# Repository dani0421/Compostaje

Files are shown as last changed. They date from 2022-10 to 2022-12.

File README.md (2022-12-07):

# Proyecto de Sistemas embebidos
Este es el repositorio del proyecto (Nombre del proyecto) de la materia de Sitemas embebidos 

## Integrantes
Daniela Valentina Amaya Vargas

Diana Patricia Cortés Nava

Julian David Escobar Jamioy

## Problemática
Cada año la cantidad de residuos organicos a nivel mundial es de 11.200 millones y contribuyen un 5% a las emisiones de gases de efecto invernadero [1], esto cada año incrementa el calentamiento global, sin contar con que poco a poco los basureros alrededor del mundo estan llegando a su maxima capacidad de desechos. La mayoria de estos residuos se generan en los hogares y generalmente no son reutilizados, es por esto que nace la idea de crear (nombre del proyecto), una basurera de desechos organicos capaz de convertir los residuos en compostaje, esto permitirá que se logren reducir las emisiones de gases de efecto invernadero reutilizando los residuos organicos y convirtiendolos en tierra para abonar las plantas del hogar e incluso las plantas de una huerta.

## Objetivos
### Objetivo General:
Desarrollar un sistema embebido que permita darle un manejo óptimo a los desechos organicos de manera cómoda y sencilla, con el fin de poder ser implementado por cualquier usuario de manera doméstica. 
### Objetivos Especificos:
* Diseñar un sistema compacto que integre diseño de PCB, programación de microcontroladores como ESP32 y diseño físico del prototipo.
* Obtener un producto final comercial, en el que se tenga en cuenta también aspectos financieros incluyendo mano de obra.
* Documentar todas las etapas del proceso de creación del proyecto hasta su finalización.

## Alcance
Elaborar un (nombre del proyecto) capaz de transformar, en cada uso, un volumen no mayor a 1.76 L de residuos orgánicos en compostaje. Contará con 3 modos de acuerdo a cuan lleno se encuentre el tambor, los cuales podrán ser elegidos según usuario vea conveniente; una vez elegido un modo, la pantalla OLED indicará la temperatura, humedad y el tiempo que aun haga falta para que el compostaje esté listo y pueda ser retirado de (nombre del proyecto). 

## Requerimientos

### Requerimientos funcionales

* Seleccionar el nivel de compostaje que el dispositivo contiene.
* Visualizar por medio de pantalla el tiempo que falta para finalizar el proceso.
* Notificar al usuario cuando los filtros requieran ser reemplazados. 
* Evitar que el dispositivo genere malos olores.
* Notificar al usuario por medio de un mensaje vía Telegram cuando se acabó el proceso de compostaje.

### Requerimientos no funcionales

* El sistema requiere de un tiempo mínimo de 24 horas para realizar un proceso.

## Diagrama de bloques

Diagrama de bloques compost(4)

## Componentes

### Optoacoplador
Servira para realizar un desacople fisico entre el ESP32 y el controlador (LN298N) de nuestros motores, debido a que su voltaje de trabajo es diferente; se hara uso de la referencia TLP281 de 4 canales.
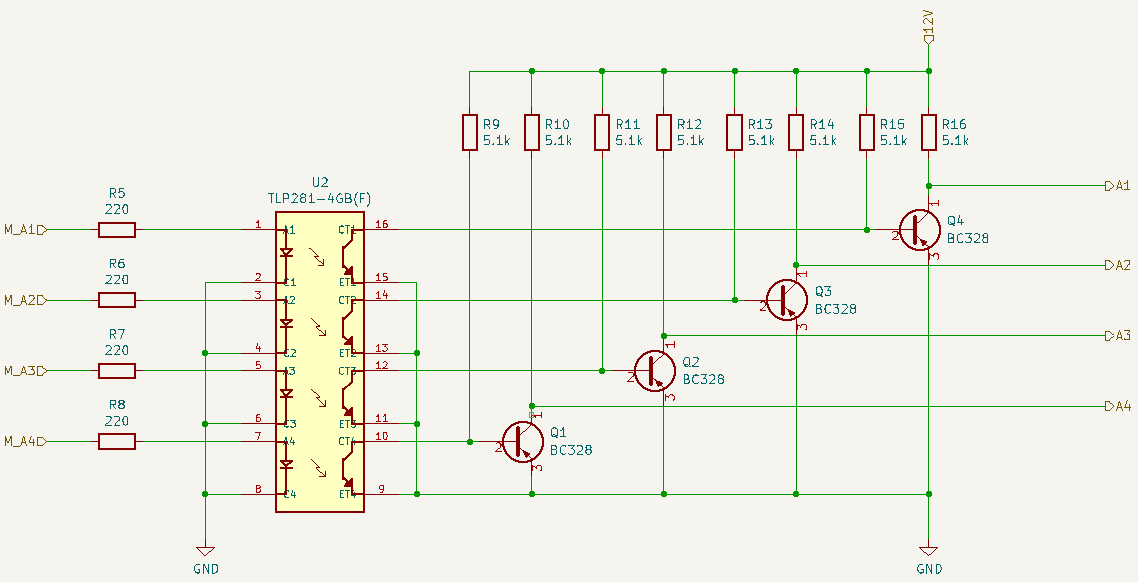
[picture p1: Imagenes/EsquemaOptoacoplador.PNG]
Esquema Optoacoplador



### Controlador de Motor
Referencia L298N que posee 4 pines de salida, teniendo en cuenta que nuestro motor es un KH56JM2U047 de bifase y con 4 pines de entrada.
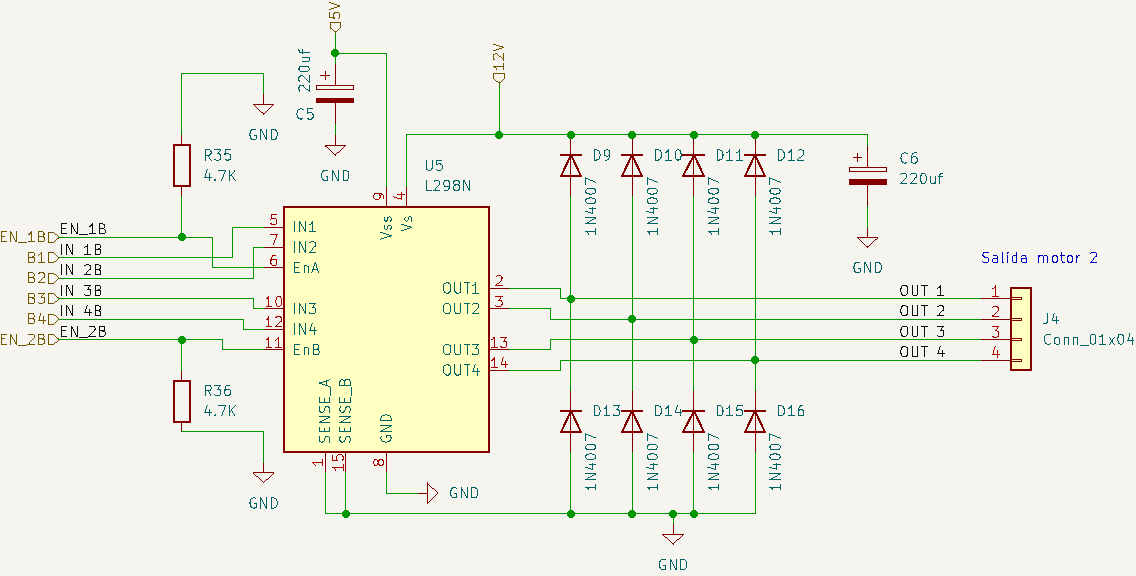
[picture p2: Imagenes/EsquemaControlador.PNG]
EsquemaControlador




### Pantalla OLED
Se usará la referencia SSD1306, la cual posee una matriz de 128x64 y cuya alimentación necesaaria es de 3.3V ([DATASHEET](https://html.alldatasheet.com/html-pdf/1179026/ETC2/SSD1306/701/6/SSD1306.html)); donde el usuario podra observar el tiempo que aun hace falta para que el compostaje este listo. Cuya dirección para I2C es 0x3C.

OLEDimagen

El SDA se conecta al pin 33 del ESP32 y el SCL al pin 36 de ESP32, cabe resaltar que en la placa no quedaran orificios para la pantalla, unicamente los pines para hacer la conexión.

### Touch
Aunque la ESP posee pines que se pueden usar como touch, se optó por hacer uso de un touch capacitivo externo, el cual nos permitirá abrir la tapa principal, que es por donde se introducira los residuos organicos junto a la tierra que posteriormente se mezclará. La referencia a usar es HW-139



### Motor Nema
Para el proceso de triturado de los residuos organicos y mezclado se usaran dos motores NEMA 17, estos son motores bipolares que pueden ser alimentados con un voltaje de 12 a 24 voltios, se opto por alimentarlos a un voltaje de 12V. 



### Servomotor

El servomotor se usara para abrir y cerrar la tapa de la basuera 


## Diseno PCB
A continuacion se muestra el diseno que se realizo para la PCB

WhatsApp Image 2022-12-06 at 11 18 50 PM
WhatsApp Image 2022-12-06 at 11 18 51 PM
WhatsApp Image 2022-12-06 at 11 18 09 PM

## Montaje fisico
Para el montaje fisico se imprimeron en 3D las siguientes piezas:

WhatsApp Image 2022-12-06 at 11 18 11 PM(2)

Luego se procedio al armado de el prototipo como se muestra en las siguientes imagenes:

WhatsApp Image 2022-12-06 at 11 18 11 PM(1)
WhatsApp Image 2022-12-06 at 11 18 10 PM
WhatsApp Image 2022-12-06 at 11 18 11 PM
WhatsApp Image 2022-12-06 at 11 18 04 PM
WhatsApp Image 2022-12-07 at 7 59 00 AM

https://user-images.githubusercontent.com/92388558/206091587-dc1af1c8-e01d-440c-9be7-15e96c51869d.mp4

## Pruebas de funcionamiento

https://user-images.githubusercontent.com/103794195/206186310-e058958a-483b-43ef-9478-b426c58254a1.mp4

## Referencias
[1] Nations, U. (2022). Datos y cifras | Naciones Unidas. Retrieved 24 August 2022, from https://www.un.org/es/actnow/facts-and-figures

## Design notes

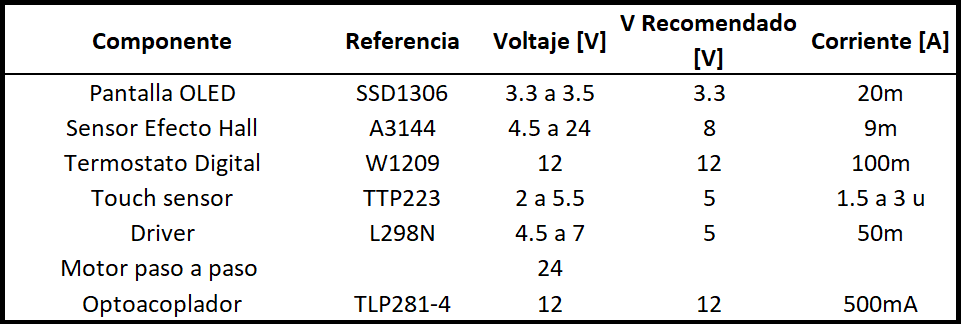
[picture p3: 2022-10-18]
Imagenes/TablaPotencia.PNG

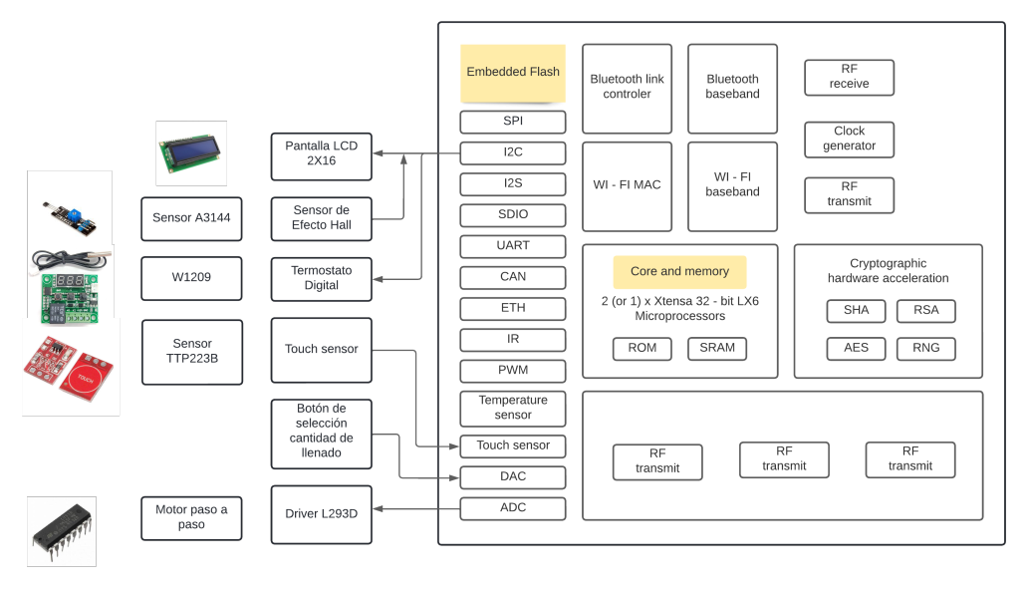
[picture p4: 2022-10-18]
Imagenes/Esquema2.PNG

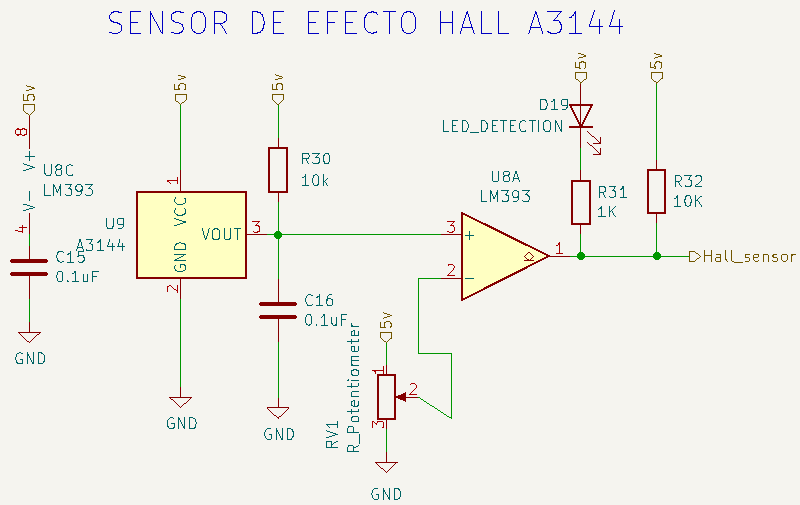
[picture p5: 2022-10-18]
Imagenes/EsquemaHall.PNG

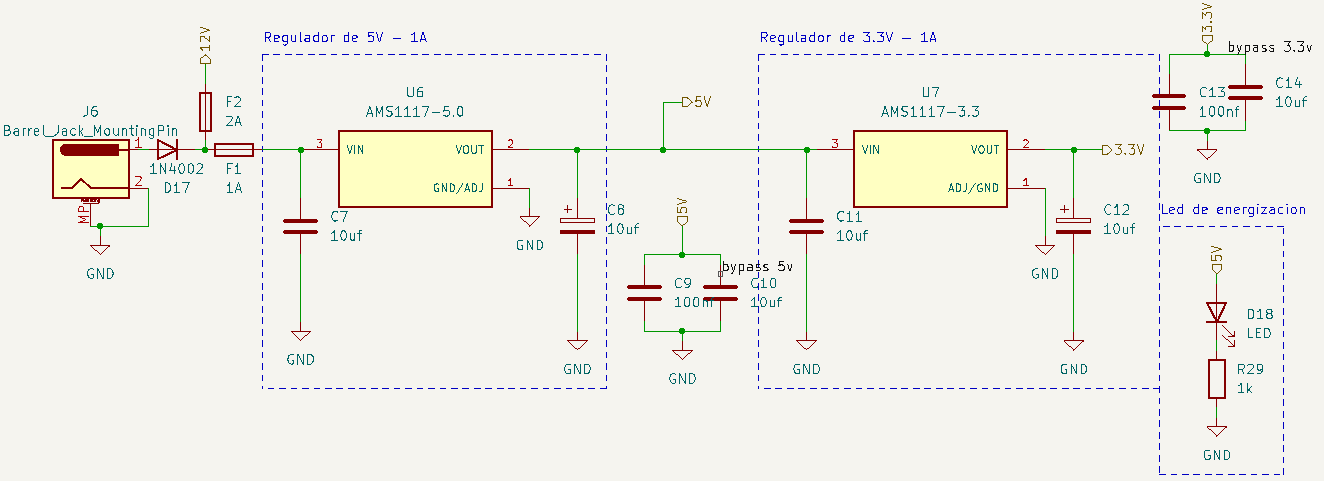
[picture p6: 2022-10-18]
Imagenes/EsquemaPotencia.PNG

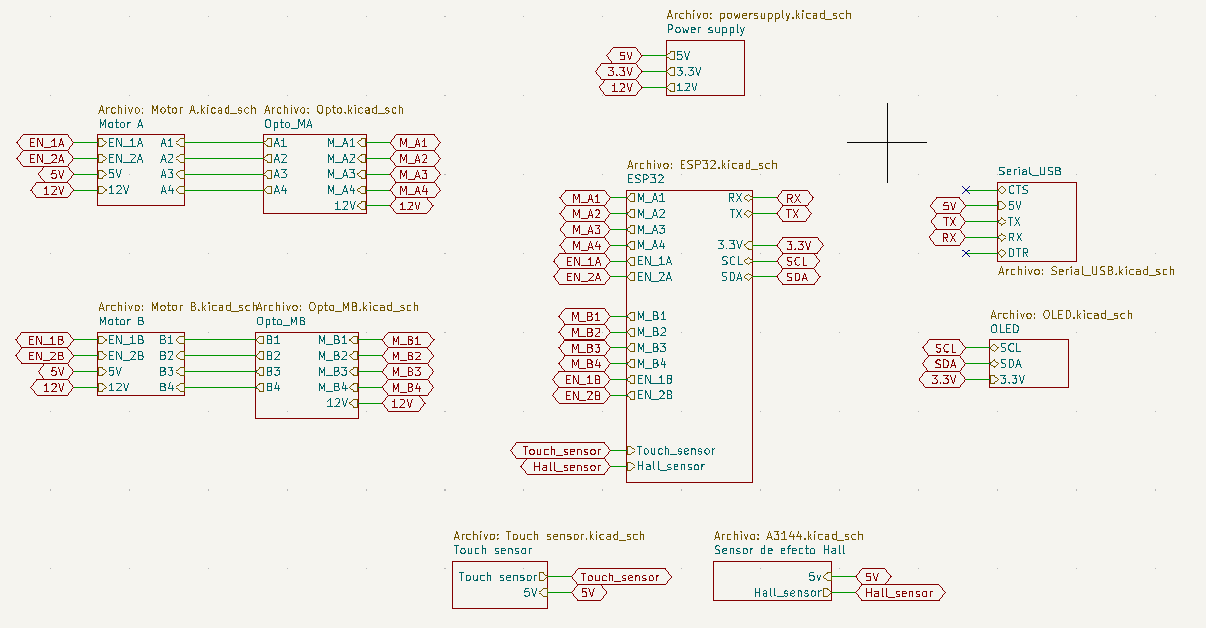
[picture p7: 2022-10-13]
Imagenes/Esquema.PNG

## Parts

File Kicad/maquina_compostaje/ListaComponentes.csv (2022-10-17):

Id | Designator | Package | Quantity | Designation | Supplier and ref
1 | C18 | C_1206_3216Metric_Pad1.33x1.80mm_HandSolder | 1 | 10uF
2 | SW2 | smd_push2 | 1 | BOOT
3 | C17,C15,C16 | C_1206_3216Metric_Pad1.33x1.80mm_HandSolder | 3 | 0.1uF
4 | R3,R2,R36,R34,R35,R33 | R_1206_3216Metric_Pad1.30x1.75mm_HandSolder | 6 | 4.7K
5 | C4,C5,C6,C3 | CP_Elec_8x10 | 4 | 220uf
6 | J2 | JST_EH_B5B-EH-A_1x05_P2.50mm_Vertical | 1 | GPIO
7 | SW1 | smd_push2 | 1 | RESET
8 | J5 | JST_EH_B3B-EH-A_1x03_P2.50mm_Vertical | 1 | TOUCH_SENSOR
9 | R4,R30,R1 | R_1206_3216Metric_Pad1.30x1.75mm_HandSolder | 3 | 10k
10 | D18 | LED_1206_3216Metric_Pad1.42x1.75mm_HandSolder | 1 | LED
11 | U9 | Allegro_SIP-3 | 1 | A3144
12 | RV1 | Potentiometer_ACP_CA6-VSMD_Vertical | 1 | R_Potentiometer
13 | J8 | JST_EH_B4B-EH-A_1x04_P2.50mm_Vertical | 1 | OLED
14 | U8 | SOIC-8_3.9x4.9mm_P1.27mm | 1 | LM393
15 | U5,U4 | TO-220-15_P2.54x2.54mm_StaggerOdd_Lead4.58mm_Vertical | 2 | L298N
16 | C2 | C_1206_3216Metric | 1 | 10uf
17 | R32 | R_1206_3216Metric_Pad1.30x1.75mm_HandSolder | 1 | 10K
18 | U1 | ESP32-WROOM-32 | 1 | ESP32-WROOM-32
19 | D19 | LED_1206_3216Metric_Pad1.42x1.75mm_HandSolder | 1 | LED_DETECTION
20 | J7 | JST_EH_B6B-EH-A_1x06_P2.50mm_Vertical | 1 | SERIAL_USB
21 | C8,C12 | CP_Elec_6.3x5.4 | 2 | 10uf
22 | J1 | JST_EH_B6B-EH-A_1x06_P2.50mm_Vertical | 1 | OTHERS
23 | J3,J4 | JST_EH_B4B-EH-A_1x04_P2.50mm_Vertical | 2 | Conn_01x04
24 | R31 | R_1206_3216Metric_Pad1.30x1.75mm_HandSolder | 1 | 1K
25 | J6 | BarrelJack_Horizontal | 1 | Barrel_Jack_MountingPin
26 | C1,C11,C14,C10,C7 | C_1206_3216Metric_Pad1.33x1.80mm_HandSolder | 5 | 10uf
27 | R29 | R_1206_3216Metric_Pad1.30x1.75mm_HandSolder | 1 | 1k
28 | R14,R16,R23,R22,R9,R21,R28,R15,R13,R25,R26,R24,R11,R12,R10,R27 | R_1206_3216Metric_Pad1.30x1.75mm_HandSolder | 16 | 5.1k
29 | D8,D1,D7,D6,D13,D11,D14,D4,D10,D15,D3,D16,D5,D12,D9,D2 | D_SOD-128 | 16 | 1N4007
30 | Q7,Q6,Q8,Q2,Q3,Q1,Q4,Q5 | SOT-23 | 8 | BC328
31 | R18,R8,R20,R19,R5,R17,R7,R6 | R_1206_3216Metric_Pad1.30x1.75mm_HandSolder | 8 | 220
32 | C13,C9 | C_1206_3216Metric_Pad1.33x1.80mm_HandSolder | 2 | 100nf
33 | U3,U2 | SO-16_5.3x10.2mm_P1.27mm | 2 | TLP281-4GB(F)
34 | U7 | SOT-223 | 1 | AMS1117-3.3
35 | F2 | Fuse_1206_3216Metric_Pad1.42x1.75mm_HandSolder | 1 | 2A
36 | D17 | D_SOD-128 | 1 | 1N4002
37 | U6 | SOT-223 | 1 | AMS1117-5.0
38 | F1 | Fuse_1206_3216Metric_Pad1.42x1.75mm_HandSolder | 1 | 1A

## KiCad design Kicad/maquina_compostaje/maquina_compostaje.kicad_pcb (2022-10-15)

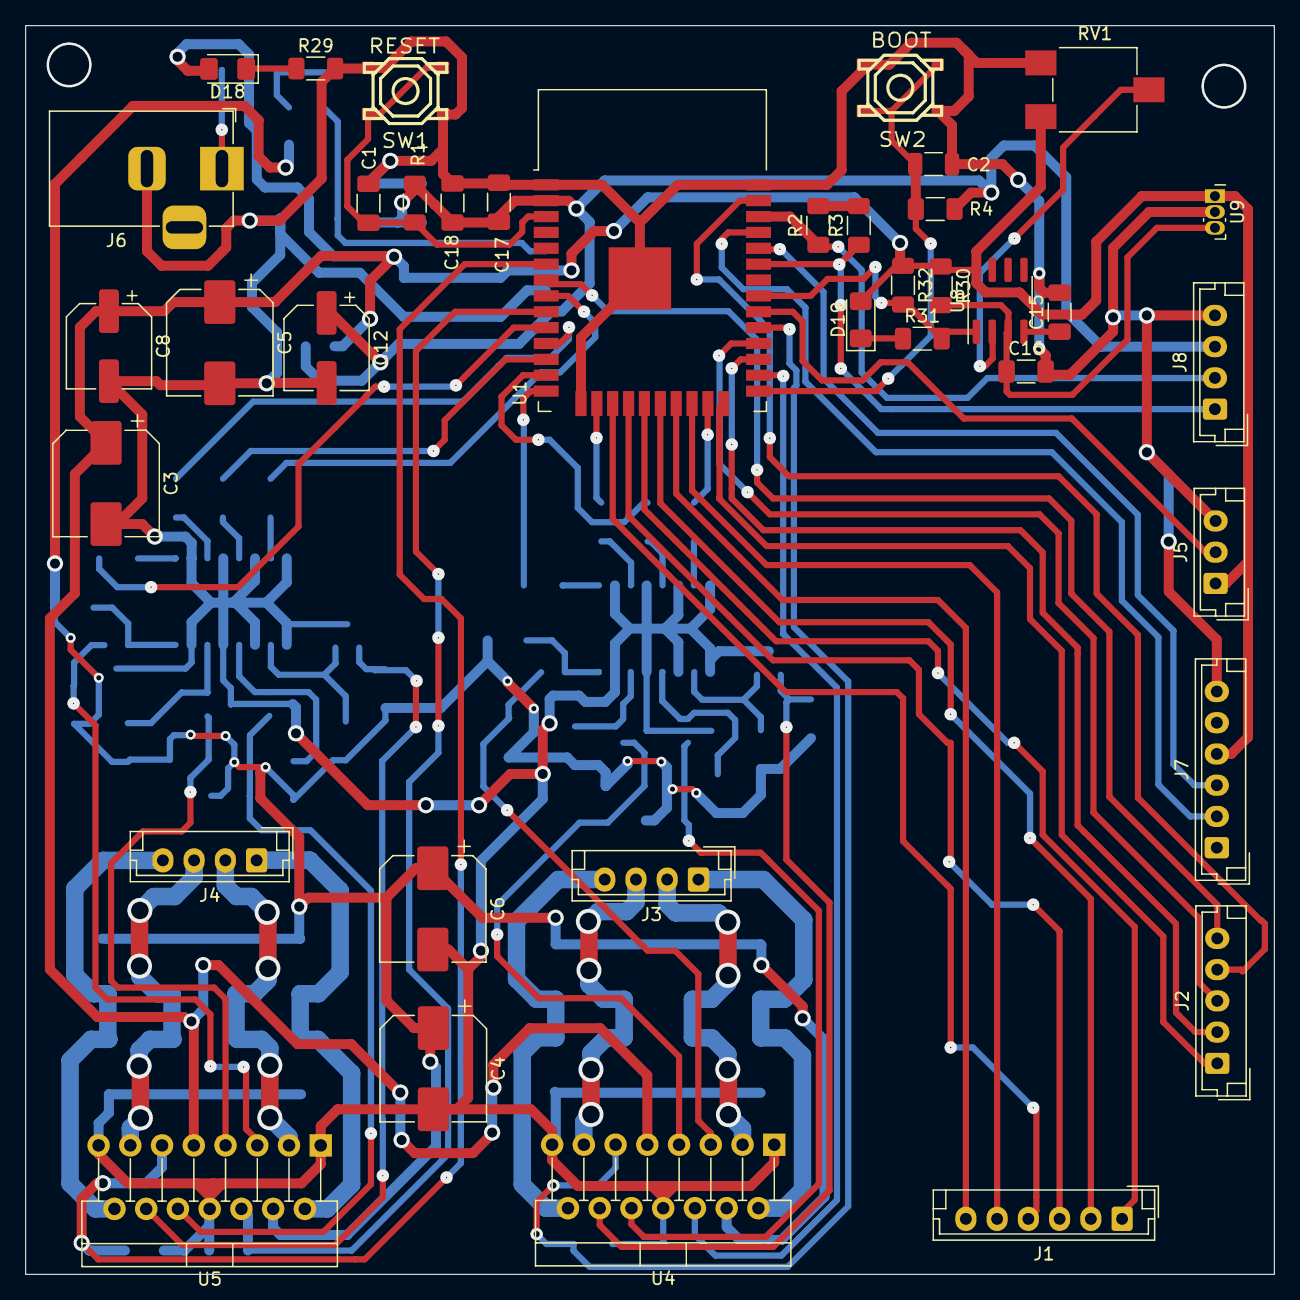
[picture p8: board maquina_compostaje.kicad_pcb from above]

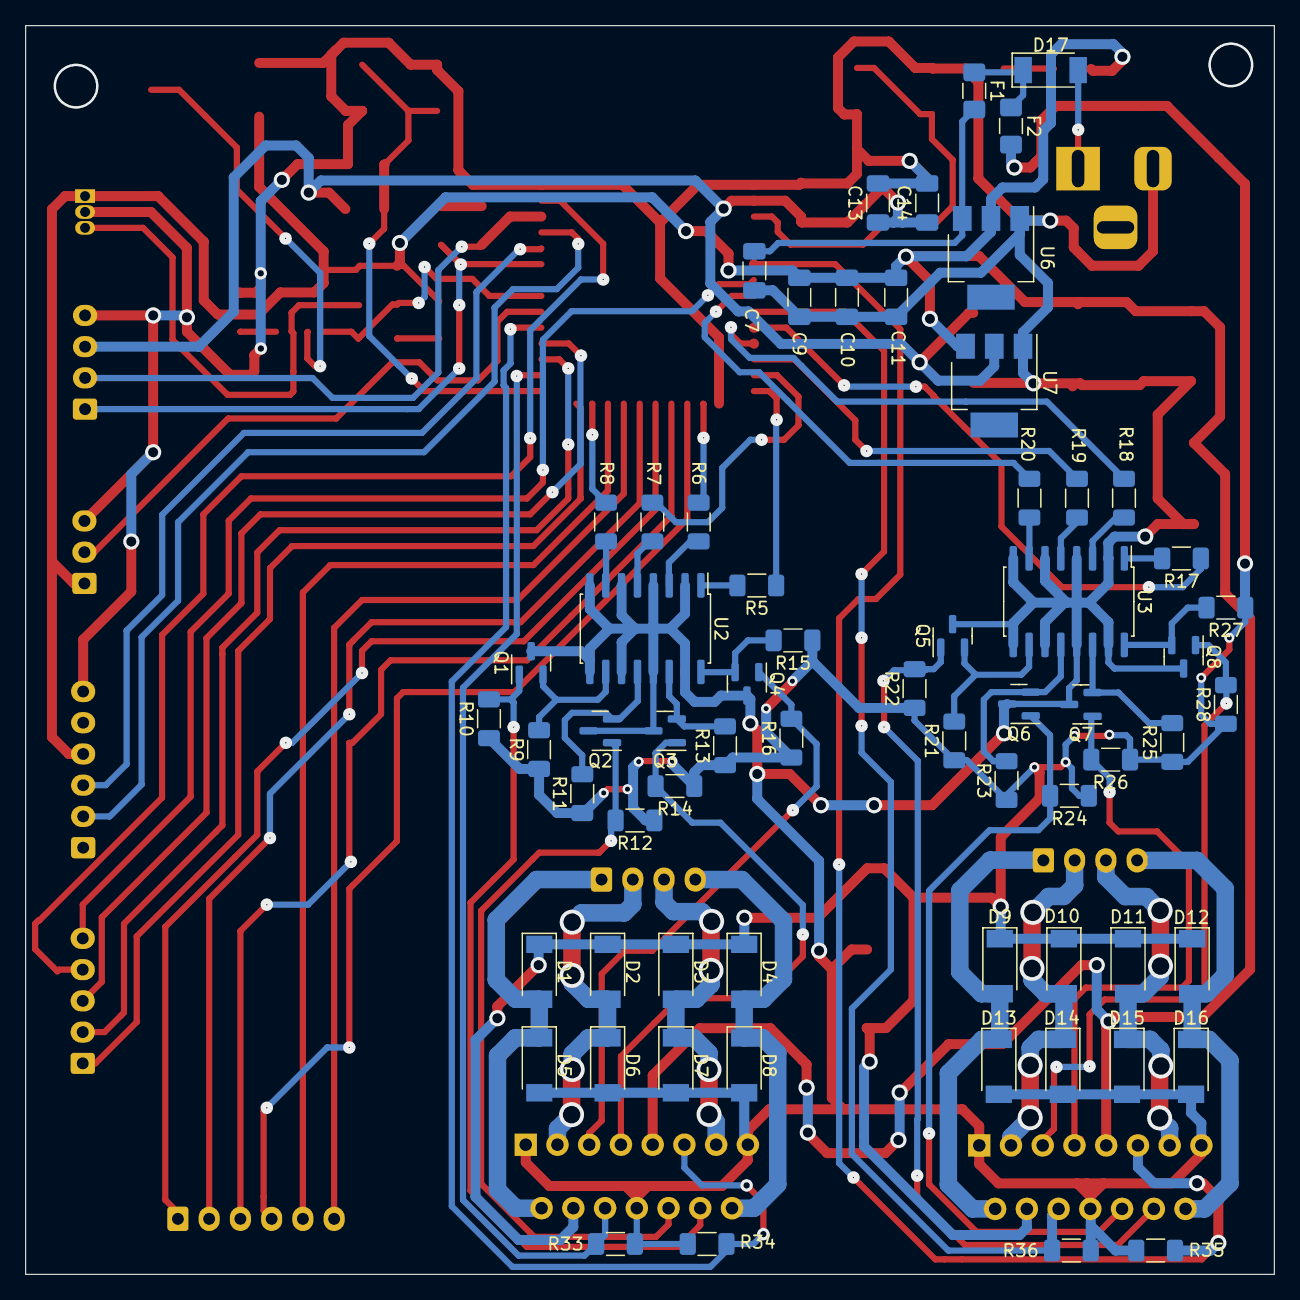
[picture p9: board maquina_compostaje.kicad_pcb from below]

Board: 2 copper layers, 99.9 x 99.9 mm, 103 parts (65 on the bottom side), 76 nets.

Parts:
C1, C7, C10, C11, C14: 10uf; C_1206_3216Metric_Pad1.33x1.80mm_HandSolder
C2: 10uf; C_1206_3216Metric
C3, C4, C5, C6: 220uf; CP_Elec_8x10
C8, C12: 10uf; CP_Elec_6.3x5.4
C9, C13: 100nf; C_1206_3216Metric_Pad1.33x1.80mm_HandSolder
C15, C16, C17: 0.1uF; C_1206_3216Metric_Pad1.33x1.80mm_HandSolder
C18: 10uF; C_1206_3216Metric_Pad1.33x1.80mm_HandSolder
D1, D2, D3, D4, D5, D6, D7, D8, D9, D10, D11, D12, D13, D14, D15, D16: 1N4007; D_SOD-128
D17: 1N4002; D_SOD-128
D18: LED; LED_1206_3216Metric_Pad1.42x1.75mm_HandSolder
D19: LED_DETECTION; LED_1206_3216Metric_Pad1.42x1.75mm_HandSolder
F1: 1A; Fuse_1206_3216Metric_Pad1.42x1.75mm_HandSolder
F2: 2A; Fuse_1206_3216Metric_Pad1.42x1.75mm_HandSolder
J1: OTHERS; JST_EH_B6B-EH-A_1x06_P2.50mm_Vertical
J2: GPIO; JST_EH_B5B-EH-A_1x05_P2.50mm_Vertical
J3, J4: Conn_01x04; JST_EH_B4B-EH-A_1x04_P2.50mm_Vertical
J5: TOUCH_SENSOR; JST_EH_B3B-EH-A_1x03_P2.50mm_Vertical
J6: Barrel_Jack_MountingPin; BarrelJack_Horizontal
J7: SERIAL_USB; JST_EH_B6B-EH-A_1x06_P2.50mm_Vertical
J8: OLED; JST_EH_B4B-EH-A_1x04_P2.50mm_Vertical
Q1, Q2, Q3, Q4, Q5, Q6, Q7, Q8: BC328; SOT-23
R1, R4, R30: 10k; R_1206_3216Metric_Pad1.30x1.75mm_HandSolder
R2, R3, R33, R34, R35, R36: 4.7K; R_1206_3216Metric_Pad1.30x1.75mm_HandSolder
R5, R6, R7, R8, R17, R18, R19, R20: 220; R_1206_3216Metric_Pad1.30x1.75mm_HandSolder
R9, R10, R11, R12, R13, R14, R15, R16, R21, R22, R23, R24, R25, R26, R27, R28: 5.1k; R_1206_3216Metric_Pad1.30x1.75mm_HandSolder
R29: 1k; R_1206_3216Metric_Pad1.30x1.75mm_HandSolder
R31: 1K; R_1206_3216Metric_Pad1.30x1.75mm_HandSolder
R32: 10K; R_1206_3216Metric_Pad1.30x1.75mm_HandSolder
RV1: R_Potentiometer; Potentiometer_ACP_CA6-VSMD_Vertical
SW1: RESET; smd_push2
SW2: BOOT; smd_push2
U1: ESP32-WROOM-32
U2, U3: TLP281-4GB(F); SO-16_5.3x10.2mm_P1.27mm
U4, U5: L298N; TO-220-15_P2.54x2.54mm_StaggerOdd_Lead4.58mm_Vertical
U6: AMS1117-5.0; SOT-223
U7: AMS1117-3.3; SOT-223
U8: LM393; SOIC-8_3.9x4.9mm_P1.27mm
U9: A3144; Allegro_SIP-3

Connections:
3.3V: C12.1, C13.1, C14.1, C17.2, C18.1, J8.3, R1.1, R4.1, U1.2 (VDD), U7.2 (VOUT)
5V: C3.1, C5.1, C8.1, C9.1, C10.1, C11.1, D18.2 (A), D19.2 (A), J5.1, J7.4, R30.1, R32.1, RV1.1, U4.9 (Vss), U5.9 (Vss), U6.2 (VOUT), U7.3 (VIN), U8.8 (V+), U9.1 (VCC)
12V: C4.1, C6.1, D1.1 (K), D2.1 (K), D3.1 (K), D4.1 (K), D9.1 (K), D10.1 (K), D11.1 (K), D12.1 (K), F2.2, R9.1, R10.1, R11.1, R12.1, R13.1, R14.1, R15.1, R16.1, R21.1, R22.1, R23.1, R24.1, R25.1, R26.1, R27.1, R28.1, U4.4 (Vs), U5.4 (Vs)
+3.3V: R2.2, R3.2
/ESP32/SCK: J1.2, U1.20 (SCK/CLK)
/ESP32/SCS: J1.1, U1.19 (SCS/CMD)
/ESP32/SD0: J1.6, U1.21 (SDO/SD0)
/ESP32/SD1: J1.5, U1.22 (SDI/SD1)
/ESP32/SD2: J1.4, U1.17 (SHD/SD2)
/ESP32/SD3: J1.3, U1.18 (SWP/SD3)
/ESP32/gpio2: J2.1, U1.24 (IO2)
/ESP32/gpio16: J2.2, U1.27 (IO16)
/ESP32/gpio17: J2.3, U1.28 (IO17)
/ESP32/gpio23: J2.4, U1.37 (IO23)
/ESP32/gpio35: J2.5, U1.7 (IO35)
/Motor A/IN 1A: Q4.1 (C), R16.2, U4.5 (IN1)
/Motor A/IN 2A: Q3.1 (C), R14.2, U4.7 (IN2)
/Motor A/IN 3A: Q2.1 (C), R12.2, U4.10 (IN3)
/Motor A/IN 4A: Q1.1 (C), R10.2, U4.12 (IN4)
/Motor A/OUT 1: D1.2 (A), D5.1 (K), J3.1, U4.2 (OUT1)
/Motor A/OUT 2: D2.2 (A), D6.1 (K), J3.2, U4.3 (OUT2)
/Motor A/OUT 3: D3.2 (A), D7.1 (K), J3.3, U4.13 (OUT3)
/Motor A/OUT 4: D4.2 (A), D8.1 (K), J3.4, U4.14 (OUT4)
/Motor B/IN 1B: Q8.1 (C), R28.2, U5.5 (IN1)
/Motor B/IN 2B: Q7.1 (C), R26.2, U5.7 (IN2)
/Motor B/IN 3B: Q6.1 (C), R24.2, U5.10 (IN3)
/Motor B/IN 4B: Q5.1 (C), R22.2, U5.12 (IN4)
/Motor B/OUT 1: D9.2 (A), D13.1 (K), J4.1, U5.2 (OUT1)
/Motor B/OUT 2: D10.2 (A), D14.1 (K), J4.2, U5.3 (OUT2)
/Motor B/OUT 3: D11.2 (A), D15.1 (K), J4.3, U5.13 (OUT3)
/Motor B/OUT 4: D12.2 (A), D16.1 (K), J4.4, U5.14 (OUT4)
EN_1A: R33.2, U1.26 (IO4), U4.6 (EnA)
EN_1B: R35.2, U1.9 (IO33), U5.6 (EnA)
EN_2A: R34.1, U1.29 (IO5), U4.11 (EnB)
EN_2B: R36.1, U1.6 (IO34), U5.11 (EnB)
GND: C1.2, C2.2, C3.2, C4.2, C5.2, C6.2, C7.2, C8.2, C9.2, C10.2, C11.2, C12.2, C13.2, C14.2, C15.2, C16.2, C17.1, C18.2, D5.2 (A), D6.2 (A), D7.2 (A), D8.2 (A), D13.2 (A), D14.2 (A), D15.2 (A), D16.2 (A), J5.3, J6.2, J7.6, J8.4, Q1.3 (E), Q2.3 (E), Q3.3 (E), Q4.3 (E), Q5.3 (E), Q6.3 (E), Q7.3 (E), Q8.3 (E), R29.2, R33.1, R34.2, R35.1, R36.2, RV1.3, SW1.1, SW1.2, SW2.1, SW2.2, U1.1 (GND), U1.15 (GND), U1.38 (GND), U1.39 (GND), U2.2 (C1), U2.4 (C2), U2.6 (C3), U2.8 (C4), U2.9 (ET4), U2.11 (ET3), U2.13 (ET2), U2.15 (ET1), U3.2 (C1), U3.4 (C2), U3.6 (C3), U3.8 (C4), U3.9 (ET4), U3.11 (ET3), U3.13 (ET2), U3.15 (ET1), U4.1 (SENSE_A), U4.8 (GND), U4.15 (SENSE_B), U5.1 (SENSE_A), U5.8 (GND), U5.15 (SENSE_B), U6.1 (GND/ADJ), U7.1 (ADJ/GND), U9.2 (GND)
Hall_sensor: R31.2, R32.2, U1.31 (IO19), U8.1
M_A1: R5.1, U1.14 (IO12)
M_A2: R6.1, U1.16 (IO13)
M_A3: R7.1, U1.13 (IO14)
M_A4: R8.1, U1.23 (IO15)
M_B1: R17.1, U1.10 (IO25)
M_B2: R18.1, U1.11 (IO26)
M_B3: R19.1, U1.12 (IO27)
M_B4: R20.1, U1.8 (IO32)
unnamed: C1.1, R1.2, SW1.3, SW1.4, U1.3 (EN)
unnamed: C2.1, R4.2, SW2.3, SW2.4, U1.25 (IO0)
unnamed: C7.1, F1.2, U6.3 (VIN)
unnamed: C15.1, U8.4 (V-)
unnamed: C16.1, R30.2, U8.3 (+), U9.3 (VOUT)
unnamed: D17.1 (K), F1.1, F2.1
unnamed: D17.2 (A), J6.1
unnamed: D18.1 (K), R29.1
unnamed: D19.1 (K), R31.1
unnamed: Q1.2 (B), R9.2, U2.10 (CT4)
unnamed: Q2.2 (B), R11.2, U2.12 (CT3)
unnamed: Q3.2 (B), R13.2, U2.14 (CT2)
unnamed: Q4.2 (B), R15.2, U2.16 (CT1)
unnamed: Q5.2 (B), R21.2, U3.10 (CT4)
unnamed: Q6.2 (B), R23.2, U3.12 (CT3)
unnamed: Q7.2 (B), R25.2, U3.14 (CT2)
unnamed: Q8.2 (B), R27.2, U3.16 (CT1)
unnamed: R5.2, U2.1 (A1)
unnamed: R6.2, U2.3 (A2)
unnamed: R7.2, U2.5 (A3)
unnamed: R8.2, U2.7 (A4)
unnamed: R17.2, U3.1 (A1)
unnamed: R18.2, U3.3 (A2)
unnamed: R19.2, U3.5 (A3)
unnamed: R20.2, U3.7 (A4)
unnamed: RV1.2, U8.2 (-)
RX: J7.2, U1.35 (TXD0/IO1)
SCL: J8.2, R2.1, U1.36 (IO22)
SDA: J8.1, R3.1, U1.33 (IO21)
TX: J7.3, U1.34 (RXD0/IO3)
Touch_sensor: J5.2, U1.30 (IO18)

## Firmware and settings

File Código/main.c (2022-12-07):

/*
 * Copyright (C) 2016 Bas Stottelaar <basstottelaar@gmail.com>
 *	AHORA ES NUESTRO ::: PROYECTO COMPOSTAJE
 * JULIAN ESCOBAR JAMIOY
 * 
 * This file is subject to the terms and conditions of the GNU Lesser
 * General Public License v2.1. See the file LICENSE in the top level
 * directory for more details.
 */

#ifndef INDEX_DRIVER_HW_I2C
#error "INDEX_DRIVER_HW_I2C not defined"
#endif

#ifndef TEST_ADDR
#error "TEST_ADDR not defined"
#endif

#ifndef SETUP_DISPLAY
#error "SETUP_DISPLAY not defined"
#endif

#ifndef TEST_PIN_RESET
#error "TEST_PIN_RESET not defined"
#endif

#include <stdio.h>


#include "periph/gpio.h"
#include "periph/i2c.h"

#include "timex.h"
#include "ztimer.h"

#include "u8g2.h"
#include "u8x8_riotos.h"

//PARA LAS TASK
#include "board.h"
#include "thread.h"
#include "periph_conf.h"

//PARA BOTON
#define touch_tapa GPIO18   //LEE EL TOUCH
#define salida_a_servo GPIO2 //POR DONDE ENVIO EL PWM DE EL SERVO QUE ABRE LA TAPA

//PARA LOS MOTORES
#define PIN1 GPIO12 
#define PIN2 GPIO13
#define PIN3 GPIO14
#define PIN4 GPIO15
#define ENA1 GPIO4
#define ENA2 GPIO5

#define PIN5 GPIO25
#define PIN6 GPIO26
#define PIN7 GPIO27
#define PIN8 GPIO32
#define ENA3 GPIO33
#define ENA4 GPIO34

//~ #define PIN1 GPIO15
//~ #define PIN2 GPIO0
//~ #define PIN3 GPIO4
//~ #define PIN4 GPIO16

int posicion_tapa=0;  //PARA SERVOMOTOR
int cuenta_atras=0;
int max_cuenta_atras=1800;
int minutos=0;
int segundos=0;
int pantalla=0;

//>>>>>>>>>DEFINO LA TAREA
char tarea_PWM_servo[THREAD_STACKSIZE_MAIN];
void *tarea_PWM_servo_thread(void *arg){ 	
	gpio_init(salida_a_servo, GPIO_OUT);
	
	while(1){
		if(posicion_tapa==0){
			gpio_set(salida_a_servo); //Enciende el PIN
			ztimer_sleep(ZTIMER_USEC,  1000U); //Tiempo que esta ON
			gpio_clear(salida_a_servo); //Apaga el PIN
			ztimer_sleep(ZTIMER_USEC, 19000U);	
			//DEBE SUMAR 20milisegundos, o 20mil microsegundos que es el periodo que recibe el servo 2000U
			
			
		}else{		
			gpio_set(salida_a_servo); //Enciende el PIN
			ztimer_sleep(ZTIMER_USEC,  2000U); //Tiempo que esta ON
			gpio_clear(salida_a_servo); //Apaga el PIN
			ztimer_sleep(ZTIMER_USEC, 18000U);		
			//DEBE SUMAR 20milisegundos, que es el periodo que recibe el servo 20.000 U
		}
	}
	return 0;
}


//>>>>>>>>>DEFINO LA TAREA 2
char tarea_flanco_subida_touch[THREAD_STACKSIZE_MAIN];
void *tarea_flanco_subida_touch_thread(void *arg){
	//DEFINIR SI ES UNA ENTRADA O UNA SALIDA
	gpio_init(touch_tapa, GPIO_IN);

    while(1){
		unsigned int estado_touch_tapa = gpio_read(touch_tapa); //PRESIONADO ES 0, en ABIERTO ES 1	
		while(!estado_touch_tapa){
			estado_touch_tapa = gpio_read(touch_tapa);
			if(estado_touch_tapa){				
				posicion_tapa= (posicion_tapa+1) %2; //HACE CAMBIO DE ESTADO EN EL PIN DE 0 A 1 o de 1 a 0;				
				cuenta_atras=0;
				//ENTERO A STRING						//ELIMINAR#######
				char text2[20];							//ELIMINAR#######
				sprintf(text2, "%d", posicion_tapa);	//ELIMINAR#######
				puts(text2);							//ELIMINAR#######
			}
		}
	}
	return 0;
	
}

//>>>>>>>>>DEFINO LA TAREA 3
char tareaCronometro[THREAD_STACKSIZE_MAIN];
void *tareaCronometro_thread(void *arg){
	div_t resultado;
		while(1){
			//~ if(posicion_tapa){
				resultado=div((max_cuenta_atras-cuenta_atras),60); //hallar resultado y residuo
				minutos=resultado.quot;
				segundos=resultado.rem;
				ztimer_sleep(ZTIMER_MSEC, 1000);
				if(cuenta_atras==max_cuenta_atras){
					posicion_tapa=0;
					pantalla=3;
				}
				cuenta_atras=(cuenta_atras+1)%(max_cuenta_atras+1);
			//~ }else{
				//~ cuenta_atras=0;
			//~ }
		}
	return 0;
}


//>>>>>>>>>DEFINO LA TAREA 4
char tareaPantalla[THREAD_STACKSIZE_MAIN];
void *tareaPantalla_thread(void *arg){
    u8g2_t u8g2;
    /* Inicializar el I2C */
    SETUP_DISPLAY(&u8g2, U8G2_R0, u8x8_byte_hw_i2c_riotos, u8x8_gpio_and_delay_riotos);
    u8x8_riotos_t user_data =
    {
        .device_index = INDEX_DRIVER_HW_I2C,
        .pin_cs = TEST_PIN_CS,
        .pin_dc = TEST_PIN_DC,
        .pin_reset = TEST_PIN_RESET,
    };
	
    u8g2_SetUserPtr(&u8g2, &user_data);
    u8g2_SetI2CAddress(&u8g2, 0x3C);
    /* initialize the display */
    puts("Initializing display.\n");
    u8g2_InitDisplay(&u8g2);
    u8g2_SetPowerSave(&u8g2, 0);
    
	//MENSAJE BIENVENIDA
	while(1){
		switch (pantalla){
			case 0:
				/* start drawing in a loop */
				puts("Drawing on screen.\n");
				u8g2_FirstPage(&u8g2);
				do{
					u8g2_SetDrawColor(&u8g2, 2);
					u8g2_SetFont(&u8g2, u8g2_font_helvB12_tf);
					u8g2_DrawStr(&u8g2, 24, 27, "Bienvenido");
				}while (u8g2_NextPage(&u8g2));
				ztimer_sleep(ZTIMER_MSEC,2000);
				pantalla=1;
			break;
		
			case 1:
			u8g2_FirstPage(&u8g2);
				do {
					u8g2_SetDrawColor(&u8g2, 2);
					u8g2_SetFont(&u8g2, u8g2_font_helvB12_tf);
					//ENTERO A STRING
					char str_minutos[20];
					char str_segundos[20];
					sprintf(str_minutos, "%d", minutos);
					sprintf(str_segundos, "%d", segundos);
					switch (posicion_tapa) {                
						case 0:
							u8g2_DrawStr(&u8g2, 28, 14, "Deposite:");//ESPACIAR PALABRAS DELTA(Y) 16
							u8g2_DrawStr(&u8g2, 4, 32, "Res. Organicos");
							u8g2_DrawStr(&u8g2, 52, 48, "Y");
							u8g2_DrawStr(&u8g2, 30, 64, "Tierra");
						break;            
						
						case 1:
							u8g2_DrawStr(&u8g2, 30, 14, "Tiempo");
							u8g2_DrawStr(&u8g2, 22, 30, "restante");                   
							u8g2_DrawStr(&u8g2, 12, 62, str_minutos);
							u8g2_DrawStr(&u8g2, 29, 60, ":");
							u8g2_DrawStr(&u8g2, 35, 62, str_segundos);
							u8g2_SetFont(&u8g2, u8g2_font_open_iconic_embedded_2x_t);
							u8g2_DrawGlyph(&u8g2, 92, 62, 0x004E);
						break;

						case 2:
							u8g2_SetFont(&u8g2, u8g2_font_open_iconic_weather_2x_t);
							u8g2_DrawGlyph(&u8g2, 20, 20, 0x0042);
						break;
					}
				} while (u8g2_NextPage(&u8g2));
				//TIEMPO DE ESPERA
				ztimer_sleep(ZTIMER_USEC, 1*US_PER_SEC);
			break;
    
			//CUANDO FINALIZA
			case 3:
				/* start drawing in a loop */
				puts("Drawing on screen.\n");
				u8g2_FirstPage(&u8g2);
				do{
					u8g2_SetDrawColor(&u8g2, 2);
					u8g2_SetFont(&u8g2, u8g2_font_helvB12_tf);
					u8g2_DrawStr(&u8g2, 24, 27, "Listo");
				}while (u8g2_NextPage(&u8g2));
				ztimer_sleep(ZTIMER_MSEC,3000);
				pantalla=1;
			break;
		}
	}
    
	return 0;
	
}


//>>>>>>>>>DEFINO LA TAREA 5
char tareaMotor[THREAD_STACKSIZE_MAIN];
void *tareaMotor_thread(void *arg){
	
	//FALTA INICIAR LOS PINES
	gpio_init(PIN1, GPIO_OUT);
	gpio_init(PIN2, GPIO_OUT);
	gpio_init(PIN3, GPIO_OUT);
	gpio_init(PIN4, GPIO_OUT);
	gpio_init(ENA1, GPIO_OUT);
	gpio_init(ENA2, GPIO_OUT);
	
	
	gpio_init(PIN5, GPIO_OUT);
	gpio_init(PIN6, GPIO_OUT);
	gpio_init(PIN7, GPIO_OUT);
	gpio_init(PIN8, GPIO_OUT);
	gpio_init(ENA3, GPIO_OUT);
	gpio_init(ENA4, GPIO_OUT);

	bool paso [4][4] ={
		{1, 0, 1, 0},
		{0, 1, 1, 0},
		{0, 1, 0, 1},
		{1, 0, 0, 1},
		
	};
	int i2=0;
	while(1){
		if(posicion_tapa==1){
			gpio_write(ENA1, 1);
			gpio_write(ENA2, 1);
			gpio_write(PIN1, paso[i2][0]);
			gpio_write(PIN2, paso[i2][1]);
			gpio_write(PIN3, paso[i2][2]);
			gpio_write(PIN4, paso[i2][3]);
			
			gpio_write(ENA3, 1);
			gpio_write(ENA4, 1);
			gpio_write(PIN5, paso[i2][0]);
			gpio_write(PIN6, paso[i2][1]);
			gpio_write(PIN7, paso[i2][2]);
			gpio_write(PIN8, paso[i2][3]);
			
			ztimer_sleep(ZTIMER_MSEC,50);
			i2=(i2+1)%4;
		}else{
			ztimer_sleep(ZTIMER_MSEC, 100);
		}
	}
	return 0;
}


int main(void)
{
	
	//Inicio la Task1 con prioridad -1
	(void) thread_create(
            tarea_flanco_subida_touch, sizeof(tarea_flanco_subida_touch),
            THREAD_PRIORITY_MAIN - 1,
            THREAD_CREATE_WOUT_YIELD | THREAD_CREATE_STACKTEST,
            tarea_flanco_subida_touch_thread, NULL, "FlancoSubida");
	

	//Inicio la Task4 con prioridad -2
	(void) thread_create(
            tareaPantalla, sizeof(tareaPantalla),
            THREAD_PRIORITY_MAIN - 3,
            THREAD_CREATE_WOUT_YIELD | THREAD_CREATE_STACKTEST,
            tareaPantalla_thread, NULL, "Pantalla");
	
	//Inicio la Task2 con prioridad -3
	(void) thread_create(
            tarea_PWM_servo, sizeof(tarea_PWM_servo),
            THREAD_PRIORITY_MAIN - 2,
            THREAD_CREATE_WOUT_YIELD | THREAD_CREATE_STACKTEST,
            tarea_PWM_servo_thread, NULL, "Servo");
	
	//Inicio la Task3 con prioridad -3
	(void) thread_create(
            tareaCronometro, sizeof(tareaCronometro),
            THREAD_PRIORITY_MAIN - 4,
            THREAD_CREATE_WOUT_YIELD | THREAD_CREATE_STACKTEST,
            tareaCronometro_thread, NULL, "Cronometro");
	
	//~ //Inicio la Task5 con prioridad -4
	(void) thread_create(
            tareaMotor, sizeof(tareaMotor),
            THREAD_PRIORITY_MAIN - 5,
            THREAD_CREATE_WOUT_YIELD | THREAD_CREATE_STACKTEST,
            tareaMotor_thread, NULL, "Motor");

    return 0;
}

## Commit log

2022-09-12 creación carpeta de diagramas en Kicad
    [sensor_efecto_hall_a3144.kicad_pcb, sensor_efecto_hall_a3144.sch]
2022-09-12 creación del diagrama esquematico del sensor A3144
    [sensor_efecto_hall_a3144.sch]
2022-09-13 Create Esquematico Driver A4988
2022-10-06 Create Diseno Kicad
2022-10-06 Diseno Kicad
2022-10-11 inicio del ruteo
    [A3144.kicad_sch, ESP32.kicad_sch, Motor A.kicad_sch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]
2022-10-13 se agregaron componentes en la parte inferior de la placa
    [ESP32.kicad_sch, OLED.kicad_sch, Serial_USB.kicad_sch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]
2022-10-15 PCB ACTUALIZADA
    [maquina_compostaje.kicad_pcb]
2022-10-17 Lista de materiales
    [ListaComponentes.csv]
